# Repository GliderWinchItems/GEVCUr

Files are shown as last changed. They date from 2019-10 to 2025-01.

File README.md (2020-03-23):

# GEVCUr
This goal of this project is to replace the GEVCU unit that control the DMOC (motor inverter) with our unit (hence the 'r') as a step towards developing the master control for the winch. The open source, source code for the GEVCU was used as a guide for dmoc_control.c.

The project is based on the STM32CubeMX, FreeRTOS, and ST DiscoveryF4 board. It uses the control panel developed for the 'mc' (Master Controller) that can be found in GliderWinchCommons (which was based on bare-metal programs).

Electric winch two motor testing 

Two motors are coupled via a Gates belt.  One motor operates in torque mode and the other acts as a regenerative brake in speed mode.  The battery bank supplies power to make up for losses.  Other instrumentation measures drive belt tension, and inverter currents, etc.

WARNING: Use at your own risk. There is a lot of code in this project,and many routines have not been reviewed with others, so bugs, errors, etc., can be expected even though it may appear to "work."

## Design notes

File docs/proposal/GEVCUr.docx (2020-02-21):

SPI and shift-register switches - spiserialparallelSW.[ch]

A. General Strategy

The spi reads from the input shift register while writing to the output shift register. The input shift register loads in parallel from switch inputs, and the output shift register drives FETs that drive LEDs. The switch inputs have pullup resistors and the switch contact closure pulls the input to ground. Therefore, open switches present a one bit. The output shift register drives a FET which pulls a LED via a resistor to gnd, so a one bit in the output turns the LED on.

The spi sends/receives two bytes (currently in the 2/20/2020 repo) then causes an interrupt. The interrupt callback deals with the logic of the switches and restarts another send/receive cycle. With the spi set to the slowest rate the interrupt rate is about 1004 cycles per 100 ms, i.e. approximately 10 cycles per ms. Net, the state of the switches are sampled at about 10K per second.

To deal with this rate, the interrupt callback handling xor’s the input half-word (16b, i.e. two bytes) with the previous half-word, producing a word with bits that are set for switch bits that have changed. If there is no change, no further processing is needed and the next spi cycle is started. If there are changes the switches with changes are updated.

Since a time source is needed for timing the debouncing the spi is used, since the spi interrupt is already present and the rate is relatively constant, the variation only due to the time variations between interrupt and restarting the next cycle. The interrupts are counted down to yield a timing rate of about 100 per sec which is used to time for switch debouncing.

The interrupt handling, therefore, 1) checks for changes in switch bits, handling only those that have changed, and 2) when the countdown counter expires, updates the timing for switches that actively being debounced.

There can be two types of switches. One is the on/off, or pushbutton type, i.e. SPST, and the other is a SPDT which appears to the spi/shift-register as a pair of on/off switches. For the switch pair the combination of the two inputs is used to determine the switch state and debouncing of a single contact is not needed, though at some point timing the indeterminate states as a hardware error check might be added.

B. Switch structs

A switch that is to be used is “instantiated” by a FreeRTOS task by calling an initialization routine. The routine adds a struct to the heap and returns a pointer for that switch to the calling task. The arguments to the initialization routine provides the specifications--

(In the following, the text between “ “ is the element name in the struct.)

(“$” designates arguments in the call to instantiate a switch.)

1. Pointer to next instantiated switch struct, i.e. linked list (“pnext”)

NULL = last on the list of instantiated switches

2. Pointer to next switch that is actively being time for debouncing (“pdbnx”)

NULL = last on the list of active debouncing switches

3. $ Task handle (“tskhandle”)

Null = use the handle of calling task.

4. $ Notification word bit (“notebit”)

This specifies the bit used when the task is notified of a switch status change.

Zero = skip notification

5. $ Switch bit position (“switchbit”)

The bit position in the spi read word for this switch.

6. $ Switch bit position1 (“switchbit1”)

The bit position in the spi read word for this switch for the second in a switch pair, If zero, then the switch is not a pair.

7. $ Type (“type”) (Redundant, unless other possibilities are conjured up.)

0 = SPST, on/off (pushbutton)

1 = SPDT, switch pair

8. Switch status not debounced (“on”)

SPST:

0 = switch closed;

1 = open

SPDT:

0 = 00 both closed *

1 = 01 combination

2 = 10 combination

3 = 11 both open *

* debounced state remains unchanged

9. Switch status debounced (“db_on”)

0 = switch closed;

1 = open

10. $ Mode for debouncing (“mode”)

Here are the current definitions. Only the first three are implemented--

#define SWMODE_NOW 0 // Immediate, w debounce minimum

#define SWMODE_WAIT 1 // Wait until debounce ends

#define SWMODE2_RS 2 // Switch pair R-S flip flop mode

#define SWMODE2_RS_00 3 // Switch pair 00 debounced

#define SWMODE2_RS_11 4 // Switch pair 11 debounced

#define SWMODE2_RS_0011 5 // Switch pair 00 & 11 debounced

11. Debounce working timing counter (“db_ctr”)

This counter counts down the spi time ticks for debouncing.

12.$ Debounce time when closing: (“db_dur_closing”)

This specifies the number of time ticks for a closing event.

13. $ Debounce time when opening: (“db_dur_opening”)

This specifies the number of time ticks for an opening event.

Example of instantiation of a pushbutton switch--

// Control Lever Fullscale Normally open. */

struct SWITCHPTR* psw_cl_fs_no = switch_pb_add(

NULL, /* task handle = this task */

0, /* Task notification bit */

CL_FS_NO, /* 1st sw see shiftregbits.h */

0, /* 2nd sw (0 = not sw pair) */

SWTYPE_PB, /* switch on/off or pair */

SWMODE_WAIT, /* Debounce mode */

SWDBMS(20), /* Debounce ms: closing */

SWDBMS(20)); /* Debounce ms: opening */

Note in the above example “SWDBMS” (SwitchDeBounceMilliseconds) is a macro that converts milliseconds into spi time ticks. The spi time tick is presently 10 ms, so values less than 10 convert to one tick. If no debouncing is to be applied, enter zero instead of the macro. Zero time ticks is handled as a special case and bypasses executing code for the debouncing.

C. Modes

Converting the spi switch bit samples into switch status is different between the the SPST and SPDT switches.

C1. SPST

The switch contacts usually bounce up open and closure, and the duration of bouncing may differ between open and closure so a debounce time is specified for each.

If the switch changes state during active debounce timing, the debounce timer is re-initialized.

There are two modes for debouncing, “SWMODE_NOW”, and “SWMODE_WAIT”. Though not a mode, a third mode is “not debounced” which is executed when the debounce time is zero. A switch bit change is not placed on the list for debounce timing and the output (debounced) state follows the switch open/close. Since debounce times for open and close are specified separately this “zero debounce” can be one or both directions.

The “now” mode the first closure changes the debounced output state and starts the debounce timing. If the switch opens and closes during the debounce timing the output state does not change. Therefore, a very short press of a pushbutton gives one output pulse of duration of the debounce timer. If the press is long the output shows closure immediately and continuously as long as the button remains closed. The logic works the same with the reverse sense of open of close, but the debounce time duration will depend on the duration specified in the instantiation call arguments.

With the “wait” mode output state does not change until the debounce period has expired. A press of a pushbutton, or multiple presses, during the debounce timing do not produce any change in the output state. At the end of the debounce time the output changes to the state of the switch. Since the debounce time is extended each time the switch changes state, rapid pressing of the pushbutton with “wait” mode will indefinitely postpone output as long as the switch transitions take place before the debounce period expires.

C2. SPDT

SWMODE2_RS

The two contacts, i.e. two switches in the spi/shift-register context, determine the change of switch state. In the static state the switch will have one contact closed and the other open. In the transition between states the both may be briefly closed, or both, depending whether the switch is BBM (Break Before Make, Form C), or MBB (Make Before Break, Form D). The BBM case both contacts go open as the switch changes state. In the MBM case both contacts are closed as the switch changes state. Since the contacts might bounce during the transition have the output state only change when there is a open|close or close|open situation and remain the state when there is open|open or close|close, the contact bounce.

If a transition state remains for a long duration that is likely to indicate a hardware failure. For example, both switches open for a long period would indicate that one or both of the switches are not connected. Both closed for a long period would indicate something missing with the pullup resistors.

Adding additional modes to the code to handle these types of situations can be added later.

D. Linked lists & bit mapping

D1. Instantiated switch list--

A “head” pointer points to the first switch struct. (NULL is when the list is empty upon bootup.) The number of switch structs possible can be none (no deboucing, task notification), to as many as there are bit positions, i.e. currently 16 SPST switches possible, or one-half the number of bit positions if all the switches are SPDT.

Individual switch status can be accessed at any time via the pointer (“p→on”) when the switch was instantiated. The word with the spi read word (“spisp_rd[0].u16”) can be read at any time, but it only has the bit status for each shift-register input and SPDT switches will show up as two separate bits, whereas “p->on” will show a number 0-3 for the four possible combinations of the SPDT switch.

D2. Debouncing list--

The “head” to this list (“struct SWITCHPTR* phddb”) is NULL when there are no switches actively debouncing. When a switch bit changes, that switch is added to the the debouncing linked list (provided the specified debouncing time is not zero). Each spi time tick counter, this linked list, if not empty, is traversed, and the debouncing working counters updated. When a counter reaches zero the logic is applied that updates the debounced switch status (“db_on”), and notifies the task, if “notebit” is not zero. A task can access “db_on” at any time via the pointer (“p->db_on”)when the switch was instantiated.

D3. Bit versus struct mapping--

An array of 16 pointers holds pointers to the switch struct so that the position in the array corresponds to the bit position of the switch, as read by the spi.

struct SWITCHPTR* pchange[NUMSWS] = {0};

The spi interrupt xor’s the newly read word with the previous, thus setting bits for switches that have changed. In a single machine cycle the CLZ (count leading zeros) assembly instruction converts the bit position in the xor’d word to the number which is then used an index into the mapping array, thus providing a fast path to the struct for dealing with the change in the switch contact status.

LAST. Items--

Miscellaneous thoughts about the topic.

Array versus heap as needed

Two ways of implementing the structs for each switch is to, 1) define the maximum possible number of structs in common memory, or 2) add structs as needed (via calloc) on the heap. If the structs are placed on the heap, they are not necessarily in consecutive memory locations. To access the structs, given the switch bit position, without a search, an array of pointers that maps bit position to struct location is needed.

However, with all possible structs pre-defined, the mapping array is not needed, saving 4 bytes per switch position, i.e. with 16 switches, 64 bytes. Another 4 bytes are saved in the struct since the list linking the structs is not needed. Net, 128 bytes. Each struct is reduced to 20 bytes. This is weighted against heap method by the number switches actually instantiated, and the number of SPST versus SPDT type switches as the SPDT switch only needs one struct on the heap.

Task versus interrupt handling

The current routine handles the switches during the interrupt. The interrupt priority is set to low priority. The processing is normally very short as most of the time there are no switches changing state and no switches requiring debounce timing. If the application has a large number of switches that change at the same time then some attention to the worst-case interrupt duration and how it might affect RTOS tasks is needed.

If the switch handling is done with a task, then each time the spi has a time tick or switch contact change it has to place the xor’d word on a queue for a task to do the handling. That assures short interrupt handling, but if some of the switches are critical, the switch handling task could be blocked by higher priority tasks. Furthermore, all the spi time ticks and changes result in task context switches.

Extending beyond 16b

Additional shift-registers can be added. This changes the word size in the routines. Beyond 32, the routine has to handle two words when doing xor’s of new versus previous readings since the CLZ instruction works on register, i.e. 32b.

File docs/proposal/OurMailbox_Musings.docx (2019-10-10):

Overview

“Mailbox” thoughts & musings, mainly as an aid to clarifying how to abstract and organize mailboxes in the context of this general project effort.

The notion of adding an ADC based mailbox to the ready-to-debug CAN mailbox code, raised a number of issues. Filtering the raw ADC readings would be expected; and might the logic apply to CAN msgs as well? Calibration is already applied to incoming CAN msgs, but need to be applied to the ADC readings. The parsing of the CAN payload is quite different than for the ADC situation where computations might be required, e.g. conversion of the internal temperature for voltage reference compensation. Filtering is a knotty issue if one considers that more than one type of filtering might be needed for the same readings, i.e. “fast” and “slow” filtering.

Online definitions of mailbox in the context of RTOS says it is a means for passing “messages”, or data exchange. For our purposes, the notion has to do more with making the values of measurements available to one or more tasks than the data where the data may not be some sensor measurement.

A. What the using task might be interested in from a mailboxes--

1. Is this a new reading since the last time I checked?

2. Is this reading “stale” i.e. too old?

3. Is this reading valid, i.e. the status?

4. Being notified when it is updated.

5. The reading filtered either/both--

a. Fast

b. Slow

c. Raw

d. Custom

6. The reading calibrated--

a. Offset

b. Scale

c. For ADC: Temperature compensated

d. For ADC: Sensor voltage compensation

7. Paired readings--

E.g. two different readings in one CAN msg, e.g. shaft speed and shaft encoder counter.

B. Characteristics Our Mailbox (OMBX?) might have--

1. Holds the latest value/reading.

Updates are made without regard to whether the ombx was accessed, i.e. overrun is not an issue.

2. Specific to some reading--

The USPS mailbox receives many different types of messages, that have the common attribute of the same destination address. This concept doesn’t apply the OMBX. E.g. a single OMBX would not combine voltage of 12v supply, drum, #1 tensions, etc. (What about “paired” readings such as shaft speed and encoder count that arrive in one CAN msg? Two maibloxes? One that will handle a float and uint32_t?)

3. Identification

A specific OMBX, or pointer to it, identifies the source of the value/reading. The source could be CAN msgs, or ADC readings, etc.

Implementing this raises the issue of mapping, i.e. a OMBX routing some incoming value/reading, e.g. a CAN msg payload, or element in an array receiving measurements from an ADC scan. These have to be converted from their native form into the common OMBX.

This issue requires some thought. Some typing to develop thinking--

To get a OMBX, e.g., 5v sensor supply voltage, a call to a routine to create an OMBX given the ADC (ADC1, 2, or 3) and ADC array index would be made and a pointer returned that points to the OMBX. The name used for that pointer would be the mnemonic for 5v sensor supply voltage. The call to the routine would include the ADC module handle, and array index. For CAN, a different create routine would be called, but the pointer returned would be the same type. The call would include the CAN control block pointer for the CAN module, CAN ID, and CAN payload type code. Again the naming of the pointer would be the mnemonic for that reading.

If more than one task tried to create the same OMBX the pointer returned would point to the same OMBX, but if notifications were specified in the call, the notification would be added to the list.

The routine creating the OBMX needs to maintain a list of OBMX pointers versus the reading source so that, e.g. a CAN msg after payload conversion can be routed to a mailbox. Similarly, the same for ADC. ADC is easy/fast because the readings are always by position in an array. CAN requires some means of a lookup on CAN module and CAN ID.

Since the number of ADC measurements can not exceed 18 (16 plus internal temp and voltage reference) an array of OMBX for all possible ADC mailboxes could be allocated, i.e. the overhead of a linked list might not be worth the effort. Where the advantage of the array is realized is in the loading of the mailboxes; the index is direct whereas with a linked list the ADC raw array would have to map into the linked list via table of pointers. The linked list would save a little sram, but add flash code.

3. Filtering

At issue is whether to build-in filtering to OMBX, or do it locally in the task. Some tasks might want slow, high filtering, e.g. readings displayed via uart/minicom for human observation, such as load-cell readings. The same readings might also be used where filtering would be fast, e.g. control loop. Should inclusion of filtering in the OMBX include provision for multiple filters.

If filters are included in OMBX, are multiple types needed? A simple one pole IIR filter is simple and easy. One could pass a reading through that filter multiple times for sharper cutoff. There has to be the intermediate storage for each pass ...

The basic OMBX structure could have a pointer to a linked list of these IIR filter structs.

If there is more than one filter, the user would have to make a call to a routine that has the OMBX pointer plus a filter pointer. The filter pointer would have to be included when the OMBX was created, so that would be passed back would be a struct.

Decimation--

If decimation is involved, then most likely notification would associated with it. However, if arrival of a reading is not driving some task, i.e. a notification is give, then task must be polling. If it is polling and checking the filtered reading, then decimation takes place if the reading update is faster than the polling, as well as a resynchronization. Net—including decimation doesn’t make sense at the mailbox level.

4. Calibration

With CAN the approach has been that calibration is done at the sensor node and the CAN msg payload is a calibrated float. With ADC, same approach could be done which requires a routine between the ADC raw readings and the OMBX. The array of ADC readings would be processed to produce an array of calibrated readings before being loaded into a mailbox.

03/07/2019 OurMailbox_Musings.docx Page 3

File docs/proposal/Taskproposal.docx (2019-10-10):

Overview

This presents some ideas on the ‘dynamometer’ project, based on STM32CubeMX, FreeRTOS, and interface & support routines developed in the ‘mxusartusbcan’ project (see ‘Brief.docx’ in ‘msusartusbcan’ directory for more detail). Some of the approaches take into account using the routines beyond the dynamometer project to the winch master controller and other CAN projects. All of this is tentative and details are likely to change as implementation progresses.

A. Infrastructure Tasks

The following outlines how these features developed in the ‘mxusartusbcan’ project are used for the ‘dynamometer’ project.

1. CanTxTask

Passes CAN msgs other tasks want to send to the interface routine (‘can_iface.c’) to the HAL CAN routine (‘stm32F4xx_hal_can’). CAN msgs are sent in CAN priority order.

The CAN msg carries the pointer to the HAL CAN module handle in “our” control block, which sends the CAN msg to the CAN1 or CAN2 modules and hence the CAN bus connected to the module.

2. CanRxTask

In ‘mxusartusbcan’ incoming CAN msgs are placed in a FreeRTOS queue by the functions in the ‘can_iface.c’ routine. For ‘dynamometer’, ‘can_iface.c’ is revised to use a circular buffer and notification to a ‘MailboxTask’ rather than a using a FreeRTOS queue. Besides lower overhead, there can be multiple “take” pointers to the circular buffer, alllowing multiple tasks can access buffered msgs. There is no overwrite protection so the buffer has to be large enough so that the “take” position in the circular buffer for the task with the most delay is not overwritten by “add”. The buffer is set during initialization for ‘can_iface.c’. The ‘take’ pointers are added and initialized by tasks, thereby allowing multiple tasks access to the buffering without the need for a predetermined number to be compiled in to the code.

CAN msgs are “added” to the circular buffer during the callbacks for RX0, RX1, plus the loopback of CAN msgs that were sent if compiled with the option set. The circular buffer is loaded under interrupt, and tasks “take” msgs from the buffer at FreeRTOS task level priority. For this project ‘MailboxTask’, described later, is the main task “taking” msgs from the circular buffer; a gateway-to-PC task would be another common task with a need for dealing with all CAN msgs.

Multiple CAN modules, i.e. CAN1, CAN2, and CAN3 (‘f446 series), is handled by implementing a circular buffer for each CAN module. Partially redundant, the CAN msg struct used in the circular buffer carries the pointer to “our” CAN control block (which includes a pointer to the STM32 CAN control block), and that essentially identifies the CAN module as well.

A time-of-arrival time-stamp in the form of the 32b DTW system counter is included in the CAN msg struct in the circular buffer. Tasks can read this DTW count and check for “stale” readings. This is covered in the description below on ‘MailboxTask’.

B. Project specific tasks

Except for the ‘defaultTask’, these tasks are created “manually”, i.e. not by STM32CubeMX, and reside in the ‘Ourtasks’ directory. STM32CubeMX provides a skeleton task in ‘main’ when the task is specified in the ‘MX setup gui and ‘main’ quickly becomes very large. Most of the code in ‘main’ concerns initialization so having tasks as separate files helps modularize the project.

1. defaultTask

Created: STM32CubeMX. Priority: osPriorityIdle (-3)

The task is always setup by STM32CubeMX when FreeRTOS is selected. It resides in ‘main’. It will be used for the lowest priority computing, such as formatting data for output monitoring on usart6 using ‘yprintf’ (wrapper with semaphores for ‘vsnprintf’), stack high water mark checking, etc.

2. ControlTask

Created: manually Priority: osPriorityNormal (0)

Handles Speed and Torque control using the readings of the two ADC readings. The ADC DMA callback does a 16 reading summation under interrupt followed by a notification. The ControlTask can then do further filtering, calibration, etc., triggered by the notification (see Task02 in ‘mxusartusbcan’).

The ControlTask sends the periodic “keepalive” notifications to the MotorControlTask. The MotorControlTask then shuts down the motors if the notifications are missed. Likewise, the MotorControlTask sending periodic commands to the DMOCs and the DMOCs shutdown if the commands are not received in time.

The ControlTask sends the polling CAN msg; 64/sec. The POD/CAN unit sends back two CAN msgs with the load-cell readings as calibrated floats.

The keepalive notifications could be combined with polling if the DMOC keepalive duration can be set to span the 1/64th sec duration.

For the Master Controller (MC) the routine is interested in readings that might be a combination of the motors, therefore polling of the parameters from the DMOCs by the ‘MotorControlTask’ would be in order.

3. MotorControlTask

Created: manually Priority: osPriorityNormal (0)

This tasks maintains the connection logic for each DMOC state, e.g. “ping” msgs from the DMOCs indicate the DMOC is operational but in a not connected state.

Notification from the ControlTask causes the MotorControlTask to send the speed & torque commands.

4. MailboxTask

Created: manually Priority: osPriorityNormal (3)

The main goal of the Mailbox task is to provide tasks with readings from CAN msgs such that the mailbox has the latest reading, plus a means for detecting if the reading is new, and/or too much time has elapsed since the last update, or a task or tasks, need immediate notification. This would be set to a high FreeRTOS task priority.

Influencing the approach in the following discussion is that it is desirable that ‘MailboxTask’ handle the Master Controller project as well as the ‘dynamometer’ and ‘dynamometer’ serves to refine and prove the approach.

From the ‘ControlTask’ viewpoint, the interest is in “readings,” not CAN msgs. Mailboxes based on readings is a knotty problem for the more general case where CAN msgs might carry more than one reading. E.g. shaft encoding carries a shaft encoder count (signed 32b int) and speed (32b float), combined into one payload since they occur at the same point in time. The CAN msg would need to update two mailboxes.

Rather than deal with the multiple readings per CAN msg issue, the CAN msgs could be limited to just one reading per CAN msg. This increases the CAN bus load a bit. In the case of battery cell voltages the inefficiency makes it a dubious tradeoff. A compromise is for the mailbox to allow for two readings.

Another complicating issue is if the control program is using a a mailbox, e.g., cable speed, it the source of the reading changes when the drum changes, i.e. the ‘MailboxTask’ would be updating the cable speed mailbox from different CAN msg IDs, conditional upon the active drum. However for the retrieve, where all drums might be active, (but in low tension, low speed), the control program would be interested in all mailboxes. This latter situation opts for multiple mailbox for the same class of reading, and the control program selects the mailbox based on active drum. (The same issue applies to multiple motors and battery banks.)

At this point, the approach to be taken is to take incoming CAN msgs; look them in a table which identifies them as associate with a mailbox. Those not found in the table are discarded. Tasks have a pointer to mailboxes and a mailbox can be used by multiple tasks, so it provides a means for distributing CAN msgs to unrelated tasks. (A separate task would be sending all CAN msgs to the PC for the gateway function, if the PC gateway is included. When all CAN msgs are to be used the ‘MailboxTask’ isn’t needed and the CAN msgs can be taken directly from the circular buffer receiving the incoming CAN msgs.) (Another consideration is the CAN bus gateway, where incoming CAN msgs on one bus are selectively sent to the other bus or buses if there are three CAN modules. This is a mailbox type of process where the CAN id has to be identified and either discarded or directed to another CAN bus.)

A CAN msg found in the table has its payload parsed, according to the code in the table. PAYLOAD_TYPE_INSERT.sql already exists and carries the name v code for the payload types (26) encountered so far. This table also has to associate the CAN msg with a mailbox. A list of mailboxes could be maintained by adding a .sql file to the database that associates a mailbox name with CANID, and payload reading. Multiple readings in a CAN msg would have multiple entries in this table. The project would have a table using the #defines generated from the database tables that specifies the mailbox name. In the case of multiple drums, there would be multiple tables of identical layout (i.e. the same struct) that can be selected by drum number.

Moving to some details about some in progress work on implementation--

Work on ‘MailboxTask’ implementation began with the a CAN msg with limited payload decoding mailbox rather than “readings” mailbox. As described above in A.2., CanRxTask, the Mailbox task gets pointer to CAN msgs on the circular buffer of incoming CAN msgs. This CAN msg has the CAN id, dlc, payload, “our” control block pointer which identifies the CAN module, hence bus, plus the 32b DTW time-of-arrival timestamp. The mailbox struct includes an msg update counter, and pointer to a linked list of notification blocks; if more than one task needs to updated when the CAN msg arrives the linked list provides the task-handle and notification bit for the each of the task notifications.

When a CAN msg is added to the circular buffer in ‘can_iface.c’, a notification to ‘MailboxTask’ is made. ‘MailboxTask’ takes a CAN msgs from the circular buffer and does a lookup in the list of CAN bus, and CAN ids. If it appears in the list, it converts the payload and loads the mailbox with the payload converted to readings, plus the time-of-arrival DTW and increments an update counter in the mailbox. If the mailbox has the task handle and notification bit setup, a notification is made.

Since there can be multiple tasks that need notification when a mailbox is updated, a linked list for each mailbox provides a means of stepping down the list making notifications for each task. For tasks that do not need a notification access can be made at any time and the time-of-arrival or update counter used to determine if the reading is stale or now. To do this each tasks needs to have the pointer to the mailbox. That pointer can be retrieved by a call to “add a mailbox”. The call to “add a mailbox” includes the CAN ID, so the initialization can check for duplicates, the existing pointer is returned and a new mailbox not created, however if a notification is desired, the call to “add a mailbox” includes the notification bit to be used it is added to the linked list.

There are several levels of initialization involved. The first is the creation of ‘MailboxTask’ which is performed in ‘main’ before the task scheduler is started. The initialization would include a call to ‘can_iface.c’ to add a “take” pointer for the circular buffer of CAN msgs. When ‘MailboxTask’ has started and is in the endless loop it receives a notification and does a ‘while’ to remove CAN msgs until it is caught up.

The list of CAN bus and CAN ids to be selected is generated by the tasks during initialization, after the task starts and before the endless loop, or after the task was created but before the scheduler started. The list is sorted so that the binary lookup can executed rapidly. For eight drums the list could in the 30-40 range. For a single drum the binary lookup wouldn’t pay. For the dynamometer, the list is probably about 6 per CAN bus and a binary search isn’t warranted. The task level initialization includes the notification bit to be used by the task if notifications are used, and as such requires that the task handle has been created, hence this is most conveniently done after the task has just started.

When a task polls, it may want to know if the mailbox reading is too old, in which case it can check the current DTW time count versus the one stored in the mailbox. Or, it may need to know if there is a new reading, in which case the task compares the mailbox update count with the previous count which was saved locally. Any number of tasks can be using the CAN mailbox in these two modes.

If the notification handle is NULL or the notification bit word zero, ‘MailboxTask’ would not execute a notification. However, if given the task and notification bit was set, the task would be notified. This would unblock the task waiting with on ‘NotifyWait’ and the mailbox would be dealt without further delay. The notification bit(s) that are found to be set when the task unblocks identify the mailbox(es) that were in the notifications.

A further detail in the implementation is to have an array of pointers to the mailbox structs (which were calloc’d). When the mailboxes are created by calls at the task level initialization, the mailbox is loaded with the CAN id and CAN control block pointer (CAN module identification), and the pointer added to the array. The array of pointers is sorted on CAN id. The array of pointers is then used for the lookup with CAN that was taken off the circular buffer. CAN msgs not in the list are simply ignored for mailbox updating.

Another possibility: Do this as two steps. The first step is to select CAN msgs for a task or set of related tasks, and have a second level deal with conversion to mailboxes, or something else. If the processor/board is handling more than one winch function then some of the tasks are not interested in some of the CAN msgs. Rather than having each function go through their list of CAN msgs for each arriving CAN msg, this approach would supply each task with only the CAN msgs of interest to the task.

Simplifications from compromises--

The pure form is to have a mailbox only contain a single reading, and be agnostic entirely to CAN msgs. With this a lot of details get push out of the “user” task and in to the infrastructure tasks. If instead of a mailbox holding just one reading, the mailbox holds the readings for a CAN msg, the naming and association of mailbox readings with CAN ids can be eliminated. That still leaves the problem of various payload formats, e.g. the reading is a float, but the four bytes for the float might start at payload[0], [1], or [2]. If the bytes preceding the float were jettisoned then a single four byte element in the mailbox would suffice. If a second four byte element is added, two readings could be accommodated and this would cover most cases. Furthermore, if the readings are all converted to ints/uints and floats and presented in a union the “user” task can access them, but needs to know which type to use. E.g. suppose during the task initialization it “adds” a mailbox, which returns a pointer to the mailbox, e.g. p_tension. The mailbox might ad accessed like this --

ften_belt = p_tension->u.f1; // Get first float

ften_mtr = p_tension->u.f2; // Get second float

This requires the using program to know more about the payload than if the mailbox was simply a single reading of ‘tension_belt’.

5. GatewayTask

Created: manually Priority: osPriorityNormal (0)

This task takes incoming CAN msgs from the circular buffer with CAN msgs; converts them to the ascii/hex format and sends them out on the high speed usart (usart2 @ 2E6 baud) to the PC . (‘gateway_CANtoPC’, used in Task03, in ‘mxusartusbcan’.)

Ascii/hex CAN msgs coming in from the PC are converted to the binary CAN format and passed on to CanTxTask for sending.

To deal with the CAN1/CAN2 issue ascii/hex format robs the low two bits from the sequence number of the CAN msg and uses that for a CAN1/2/3 identifcation (STM32F4 series has two CAN modules, and the STM32F7 has three) . NOTE: this requires some modification of ‘cangate’ to either have a CAN1/2/3 version, or way to avoid the original ‘cangate’ from flagging a sequence number error.

An alternative is to use the gateway to the PC in a one CAN bus mode and avoid the CAN1/2 issue, but requires two gateways or gatewayfunctions (i.e. one could run two usarts to the PC, each carrying traffic for one CAN bus).

Use of the usb CDC (virtual com port) for gateway purposes requires some additional work, as the buffering/interrupt/polling is somewhat different with the STM HAL routine for usb-cdc and the usart routines.

‘dynamometer’ STM32CubeMX project Page 6

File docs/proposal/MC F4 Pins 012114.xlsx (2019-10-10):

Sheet: Sheet1
Use | Ports | Our Use Function | Board Function 1 | P1 | P2 | Other Functions - Comments
Input Switches and Output LEDs (GP and SPI) | PB12 | SPI2_NSS | Free I/O | 36 |  | JTDI/, SPI3_NSS/, I2S3_WS/, TIM2_CH1_ETR/, SPI1_NSS
 | PB13 | SPI2_SCK/ | Free I/O | 37
 | Other functions of PB3: JTDO/, TRACESWO/, SPI3_SCK/, I2S3_CK/, TIM2_CH2/, SPI1_SCK
 | PB14 | SPI2_MISO/ | Free I/O | 38
 | PB15 | SPI2_MOSI | Free I/O | 39
ADCs (3 allocated) | PC1 | ADC123_IN11 | Free I/O | 7
 | PC2 | ADC123_IN12 | Free I/O | 10
 | PC4 | ADC123_IN14 | Free I/O | 20
CANbus | PD0 | CAN1_RX | Free I/O |  | 36
 | PD1 | CAN1_TX | Free I/O |  | 33
UART (Bootloader) | PA9 | USART1_TX | VBUS_FS |  | 44 | Bootloader assumes serial loader is on PA9 & PA10 - conflicts with USB
 | PA10 | USART1_RX | OTG_FS_ID |  | 41
UART (GPS) | PA2 | USART2_TX | Free I/O | 14
 | PA3 | USART2_RX | Free I/O | 13
UART (LCD) | PD8 | USART3_TX | Free I/O | 40
 | PD9 | USART3_RX | Free I/O | 41
GPS 1PPS | PA1 | TIM5_CH2 | Free I/O | 35
Beeper | PB8 | TIM10_CH1 | Free I/O |  | 43
PWM (Contactor) | PE5 | TIM9_CH1 | Free I/O |  | 14
PWM (Panel Dim) | PE6 | TIM9_CH2 | Free I/O |  | 11
Audio (ISI and SPI) | PB6 |  | Audio_SCL
 | PB9 |  | Audio_DSA
 | PC7 |  | I2S3_SCK
 | PC10 |  | IS23_SCK
 | PC12 |  | IS23_SD
 | PA4 |  | I2S3_WA
 | PD4 |  | Audio_RST
 | PC3 |  | PDM_OUT
 | PB10 |  | CLK_IN
Accelerometers | PA7 |  | SPI1_MOSI
 | PA5 |  | SPI1_SCK
 | PE0 |  | MEMS_INT1
 | PE1 |  | MEMS_INT2
 | PE3 |  | CS_I2C/SPI
 | PA6 |  | SPI1_MOSI
USB_OTG | PC0 |  | OTG_FS_PowerSwitchOn
 | PA9 |  | VBUS_FS
 | PA10 |  | OTG_FS_ID
 | PA11 |  | OTG_FS_DM
 | PA12 |  | OTG_FS_DP
 | PD5 |  | OTG_FS_PverCurrent
LED (Green) | PD12 |  | GPIO
LED (Orange) | PD13 |  | GPIO
LED(Red) | PD14 |  | GPIO
LED(Blue) | PD15 |  | GPIO
Reset PB | NRST |  | NRST
User PB | PA0 |  | GPIO
Denotes a possible conflict
Check appropriate timers and channels have been used
Last Update: 1/21/2014

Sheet: Sheet2
PA1
PA10
PA10
PA11
PA12
PA15
PA2
PA2
PA3
PA3
PA4
PA5
PA6
PA7
PA8
PA9
PA9
PB10
PB11
PB3
PB4
PB5
PB6
PB9
PC0
PC10
PC12
PC3
PC3
PC4
PC7
PD0
PD1
PD10
PD4
PD5
PD8
PD9
PE0
PE1
PE10
PE11
PE12
PE13
PE14
PE3
PE7
PE8
PE9

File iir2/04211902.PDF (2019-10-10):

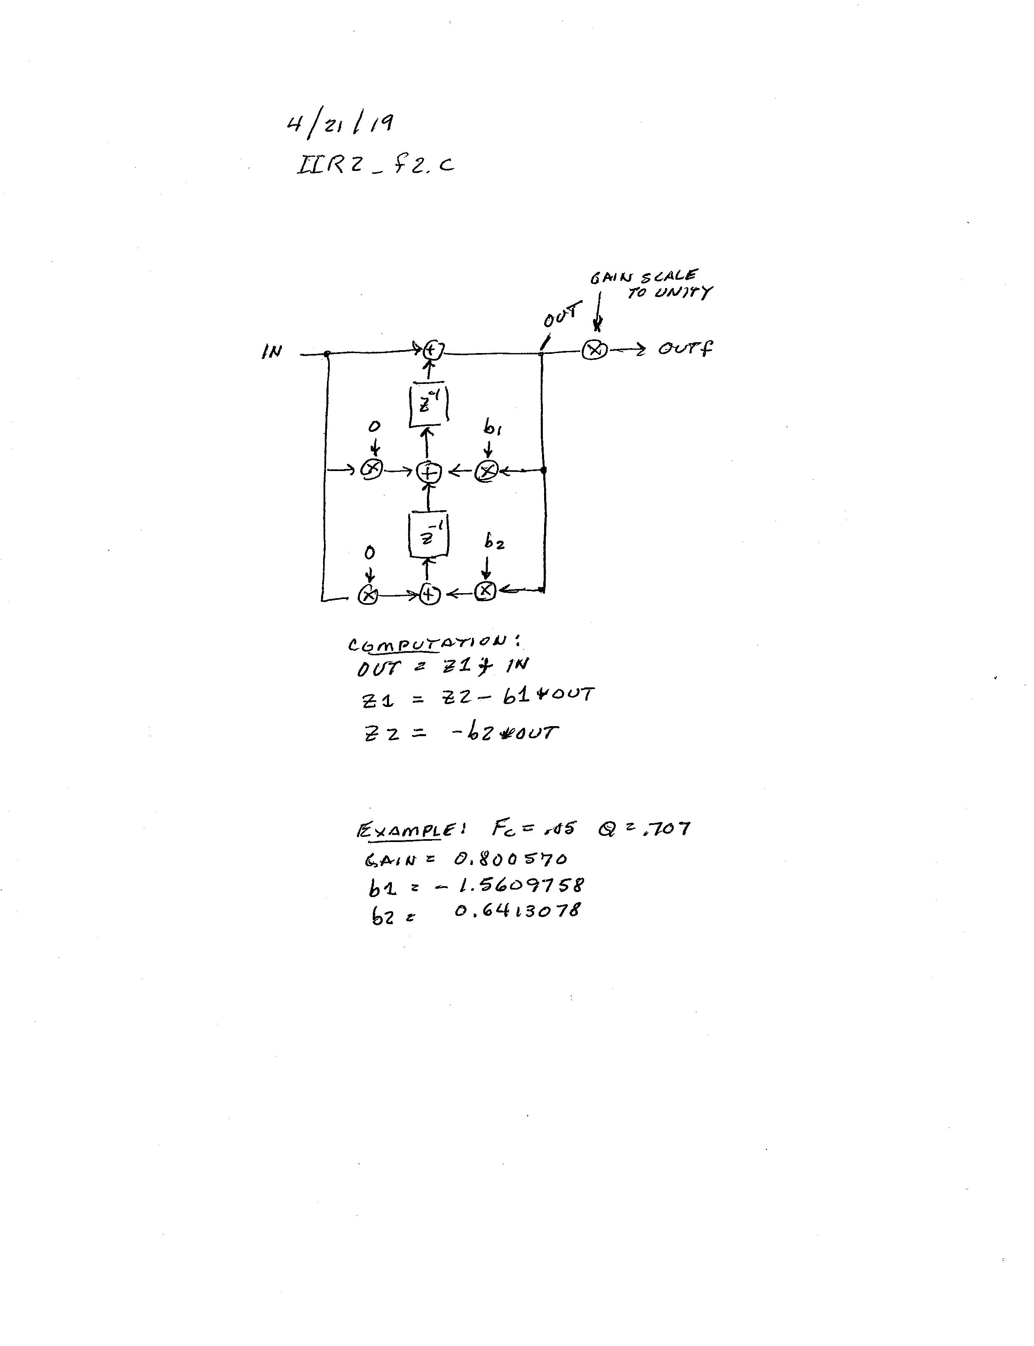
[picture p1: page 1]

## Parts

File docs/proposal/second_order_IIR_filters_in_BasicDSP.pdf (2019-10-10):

## Second-order IIR filters in BasicDSP (http://www.google.com/search?q=basicDSP)

by Niels A. Moseley PE1OIT

Second-order filters offer a sharper frequency response compared to the first-order filter. First order filters, which have a 6 dB per octave slope, are often used for quick-and-dirty smoothing. If you want a steeper slope, such as 12 dB per octave or higher, you need a higher order filter.

A simple way to achieve a higher order is to put two first-order filters in series. This is similar to putting two analog RC filters in series. Unfortunately, this isn't the best filter you can make, given the number of components. Better filters (fewer components) can be made by including an inductor L, which leads to an RLC filter.

The digital equivalent of an RLC filter is the second-order IIR filter:

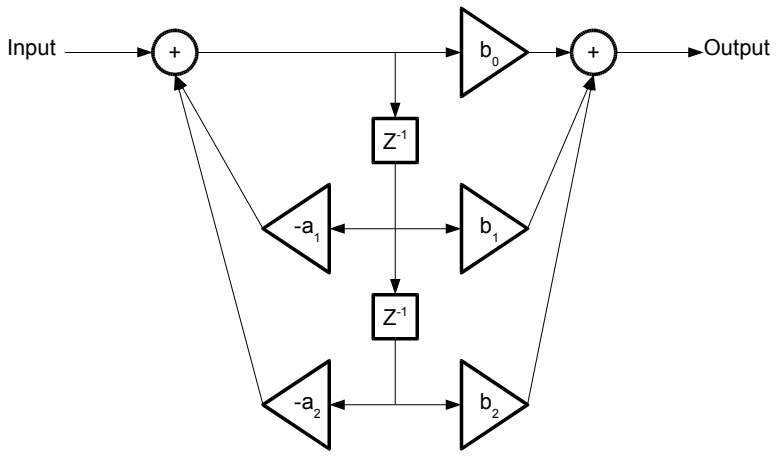
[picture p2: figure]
Input; Output

The 'Z⁻¹' blocks are a 1-sample delay. The following BasicDSP script implements this filter:

temp = f_in - a1*state1 - a2*state2
f_out = b0*temp + b1*state1 + b2*state2
state2 = state1
state1 = temp
,where 'state1' and 'state2' are the values stored in the 1-sample delay blocks. The input and output of the filter are 'f_in' and 'f_out', respectively.

For lowpass filters, the filter coefficients (a1, a2, b0, b1 and b2) can be calculated using the following formulas [1]:

pi = 3.1415927
w0 = 2*pi*f0/FS; (where f0 is the desired cutoff frequency, and FS is the sample rate)
alpha = sin(w0)/(2*Q); (where Q is typically 0.5*sqrt(2)=0.707)
b0 = (1–cos(w0))/(1+alpha)
b1 = 2*b0
b2 = b0
a1 = -2*cos(w0)/(1+alpha)
a2 = (1-alpha)/(1+alpha)

Combining the filter and the calculating of the filter coefficients, we can make a second order filter where the cutoff frequency f0 is settable through slider1:

samplerate = 44100;
f_in = in;

; calculate filter coefficients w0 = 3.1415927*slider1
alpha = sin(w0)/(2.0*0.707) b0 = (1-cos(w0))/(1+alpha)
b1 = 2*b0
b2 = b0
a1 = -2*cos(w0)/(1+alpha)
a2 = (1-alpha)/(1+alpha)

; calculate filter
temp = f_in - a1*state1 - a2*state2 f_out = b0*temp + b1*state1 + b2*state2 state2 = state1
state1 = temp

out = f_out * 0.1
Here's a screenshot of the filter spectrum (input = impulse & slider1 = 0.2476):

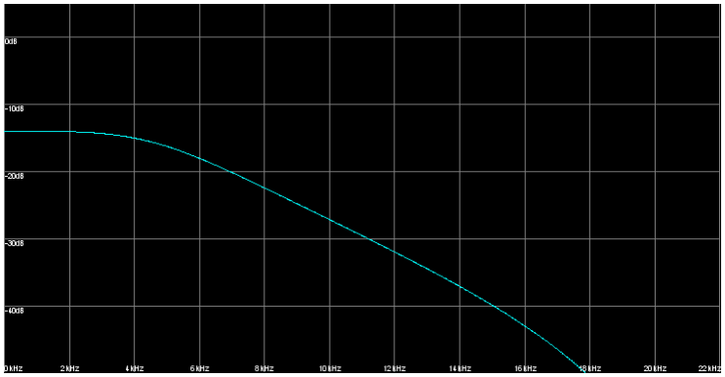
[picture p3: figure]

References:

[1] Filter design equations http://www.musicdsp.org/files/Audio-EQ-Cookbook.txt

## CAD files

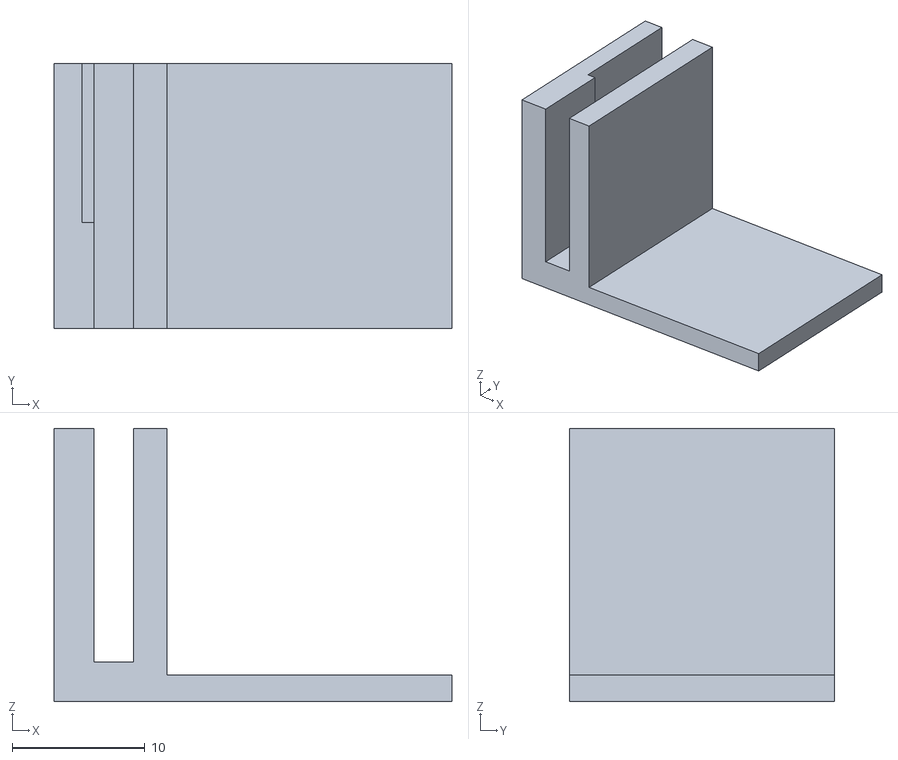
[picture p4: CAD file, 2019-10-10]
hw/openscad/ftdi_clip.stl
30.0 x 20.0 x 20.6

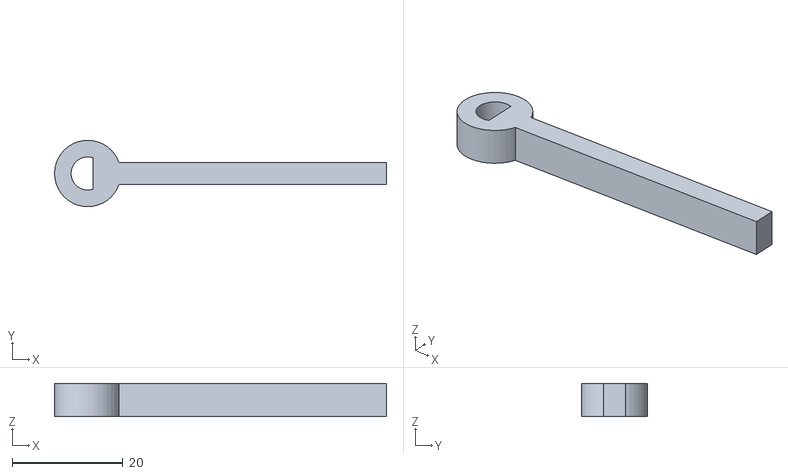
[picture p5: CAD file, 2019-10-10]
hw/openscad/pot_mnt2lvr.stl
60.0 x 12.0 x 6.00

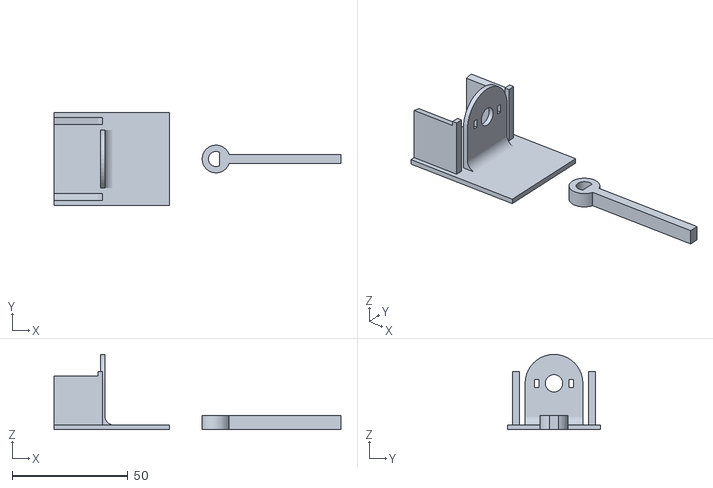
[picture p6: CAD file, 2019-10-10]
hw/openscad/pot_mnt2.stl
124.0 x 40.0 x 32.5

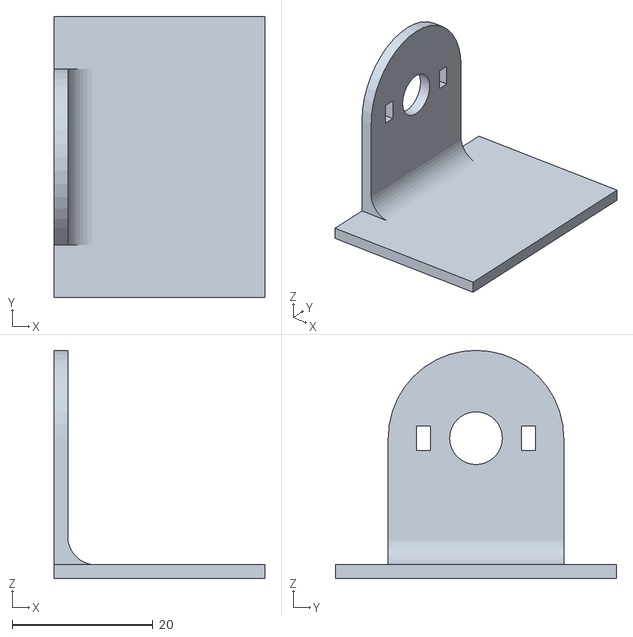
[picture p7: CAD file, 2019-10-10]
hw/openscad/pot_mnt.stl
30.0 x 40.0 x 32.5

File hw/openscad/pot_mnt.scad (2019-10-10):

/* File: pot_mnt.scad -- Stacked
 * Clip for pot mount for Control Panel simulator
 * Author: deh
 * Latest edit: 20191002
 */

include <../../../../git_3D/scad/library_deh/deh_shapes.scad>

 $fn = 40;
 
 thick = 2.0;
 
 /* ***** fillet *****
 * r = radius of fillet
 * l = length of fillet
 fillet (r,l);
*/
module fillet(r,l)
{
   difference()
   {
     union()
     {
       cube([2*r,2*r,l]);
     }
     union()
     {
       translate ([r,r,0])
           cylinder(d = 2*r + 0.1, h = l, center = false);
       translate([r,0,0])
           cube([r,2*r,l],center = false);
       translate([0,r,0])
           cube([2*r,r,l],center = false);
     }
   }
}

module pot_mnt (a)
{
    offset = 9-1.5;    

	translate(a)
		/* ***** eyebar *****
 * rounded bar with hole in rounded end
 * module eye_bar(d1, d2, len, ht)
d1 = outside diameter of rounded end, and width of bar
d2 = diameter of hole in end of bar
*/  
    difference()
    {
        union()
        {
            eye_bar(25, 7.5, 20, 2);
            
            translate([18,12.5,2])
            rotate([90,-90,0])
            fillet(4,25);
        }
        union()
        {
            translate([0,offset,0])
                cube([3.5,2.0,20],center=true);
            translate([0,-offset,0])
                cube([3.5,2.0,20],center=true);

        }
    }
}

module plat(a)
{
    translate(a)
        cube([30,40,2],center=false);
}

rotate([0,90,0])
    pot_mnt([-20,0,0]);

plat([0,-20,0]);

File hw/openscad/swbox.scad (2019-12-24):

/* File: swbox.scad
 * Box to hold perfboard with shift register w leds and switch header
 * Author: deh
 * Latest edit: 20191214
 */
 
 $fn = 40;
 
 // Perfboard dimensions
 pbdel = 0.5;  // A little extra
 pbx  = 80 + pbdel; 
 pby  = 40 + pbdel;
 pbz  = 1.5;  // board thickness
 pbz1 = 4.2;  // bottom to top of wiring
 
// Box 
 boxwall = 6;
 boxfloor = 4;
 boxx = pbx + boxwall*0.5;
 boxy = pby + boxwall*0.5;
 boxz = 24;
 
 // Main box cutout
 boxqx = pbx - boxwall*0.5;
 boxqy = pby - boxwall*0.5;
 
 // Switch cable cutout
 swcofx = 37;
 swcofz =  2;
 swcx = 6;
 swcz = 20;
 
 // spi cable cutout
 spiofx = 42;
 spiofz =  2;
 spix = 20;
 spiz = 10;
 
 // Post height
 pstz = boxz; // Height
 pstd = 6;  // Diameter
 paa = 1.1; // Post center offset
 
 
 module post(a)
 {
     translate (a)
     {
        translate([0,0,boxz-pstz])
        difference()
        {
            union()
            {   
                cylinder(d=pstd,h = pstz,center=false);
            }
            union()
            {
                translate([0,0,pstz-30])
                cylinder(d=2.9,h=60,center=false);
            }
        }
    }
 }
 
 module mainbox()
 {
     difference()
     {
         union()
         {
             cube ([boxx,boxy,boxz],center=false);
             post([    -paa,    -paa,0]);
             post([boxx+paa,    -paa,0]);
             post([boxx+paa,boxy+paa,0]);
             post([    -paa,boxy+paa,0]);
         }
         union()
         {
             // Main cutout
             translate([boxwall*0.5,boxwall*0.5,boxwall*0.5])
                cube([boxqx,boxqy,50],center=false);
             
             // Recess for perf board
             translate([boxwall*.25,boxwall*.25,boxz-pbz])
                cube([pbx,pby,50],center=false);
             
             // Switch cable
             swcq = boxfloor + swcofz;
             translate([boxwall*.25+swcofx,-4,swcq])
                cube([swcx,20,swcz],center=false);
             
             // spi cable
//             spiq = boxfloor + spiofz;
//             translate([boxwall*.25+spiofx,boxy-8,spiq])
//                cube([spix,30,spiz],center=false);
             
         }
     }
 }
 cvrz   = 4;      // Cover thickness
 cvrofx = 10 + boxwall*.25; // pushbutton window offset
 cvrofy = 25 + boxwall*.25; // pushbutton window offset
 cvrx   = 60;    // Length of pushbutton window
 cvry   = 10;    // Width of pushbutton window
 cvrdel = 2.5;   // Overlap a edge
 
 module cvrpost(a)
 {
     translate (a)
     {
        translate([0,0,0])
        difference()
        {
            union()
            {   
                cylinder(d=pstd,h = cvrz,center=false);
            }
            union()
            {
                translate([0,0,-.5])
                cylinder(d=3.2,h=8,center=false);
            }
        }
    }
 }
 cvrw = 1.5;
 cvrlj = 2.0;
 cvrlh = cvrz + cvrlj;
 
 module cvrlip(a,r,l)
 {
      translate (a)
     {
        translate([0,0,cvrlj])
        difference()
        {
            union()
            {   
                translate([0,0,0])
                cube([l,cvrw,cvrlh],center=true);
            }
            union()
            {
            }
        }    
    }
 }
 
 // Toggle switch hole in cover
module togglehole(a)
{
   translate(a)
    cylinder(d = 6.4, h = 20, center=true);
} 
 
 module cover(a)
 {
     translate(a)
     {
         difference()
         {
             union()
             {
                cube ([boxx,boxy,cvrz],center=false);
                cvrpost([    -paa,    -paa,0]);
                cvrpost([boxx+paa,    -paa,0]);
                cvrpost([boxx+paa,boxy+paa,0]);
                cvrpost([    -paa,boxy+paa,0]);
                 
//cvrlip([boxx/2,-cvrw,0],[0,0,0],boxx-2*boxwall-8);                 
             }
             union()
             {
                // Recess in cover
//                translate([boxwall*.25+cvrdel*.5,boxwall*.25+cvrdel*.5,0])
//                    cube([pbx-cvrdel,pby-cvrdel,cvrz-1.5],center=false);
                 
                // pushbutton plate window
                 translate([cvrofx,cvrofy,-1])
                    cube([cvrx,cvry, 30],center=false);
                
                // Holes for toggle switches
                 inc = 18; qx = (pbx - 3*inc)/2; qy = 13; 
                 togglehole([qx+(0*inc),qy,0]);
                 togglehole([qx+(1*inc),qy,0]);
                 togglehole([qx+(2*inc),qy,0]);                 
                 togglehole([qx+(3*inc),qy,0]);
             }
         }
     }
 }

 
 pinx = 7.0;    // sw pin spacing x direction
 piny = 4.4;    // sw pin spacing y direction
 
 swplatex = 10.0 ;  // width
 swplatey = 8.0;
 sidey = 15.0;
 
 pwinx = 1.8;
 pwiny = 1.5;
 
 module pbhole(a)
 {
     translate(a)
     {
        cube([pwinx,pwiny,20],center=true);
     }
 }
 module pbholes(a)
 {
     translate(a)
     {
        pbhole([   0,   0, 0]);
        pbhole([pinx,piny, 0]);
        pbhole([pinx,   0, 0]);
        pbhole([   0,piny, 0]);
     }
 }
 
pbhx = 70;
pbhy = 20;
pbhz = 1.4;
 module pbplate(a)
 {
hofx = 6;
hofy = 8;     
incx = 16;
     
     translate(a)
     {
         difference()
         {
            cube([pbhx,pbhy,pbhz],center=false);
             
            union()
            {
             pbholes([hofx+0*incx,hofy,0]);
             pbholes([hofx+1*incx,hofy,0]);
             pbholes([hofx+2*incx,hofy,0]);
             pbholes([hofx+3*incx,hofy,0]);             
            }
        }
     }
 }
 
// mainbox();
 
// rotate([180,0,0])
//   cover([0,0,35]);
 
 pbplate([10,20,45]);

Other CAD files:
hw/openscad/ftdi_clip2.stl
hw/openscad/pot_mnt2.scad
hw/openscad/ftdi_clip.scad
hw/openscad/ftdi_clip2.scad

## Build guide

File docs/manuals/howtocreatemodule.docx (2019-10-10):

# GEVCU

Generalized Electric Vehicle Control Unit

# Programmer Checklist

# For Adding Object Modules to the

# GEVCU Software

The Generalized Electric Vehicle Control Unit software is open source and object oriented. It was originally developed to control the Azure Dynamics model 645 Digital Motor Controller (DMOC) – a 3-phase inverter/controller used with the Siemens 1PV5134 motor on the Azure Dynamics eTransit Connect.

The DMOC645 was CAN controlled and did not feature any inputs for throttle, brake or other inputs and outputs. The eTransit Connect Vehicle Control Unit (VCU) performed that duty. Lacking the VCU, we had to develop a VCU from scratch capable of providing the necessary CAN messages to the DMOC645 to in turn control the motor.

The concept of a GENERALIZED VCU specifically for electric vehicles derived from the many different types of cars that would be converted to electric drive using this drive system. But from the beginning we saw the need to drive other types of controller/inverters and indeed interact with other devices such as chargers, DC-DC converters, and battery management systems.

So a central tenet of the GEVCU was a very object oriented approach that would easily allow the addition of new classes and new objects to accommodate different equipment. The goal of course to limit software changes to just the additional object added to accommodate the new equipment.

Some wins and some losses. Indeed GEVCU now supports the BRUSA drive train, the CODA/UQM drive train, and more are envisioned and already a series of chargers, BMS, and other devices have been added.

But along the way, we encountered several targets of opportunity that were just two good to pass on, that tend to complicate the easy addition of object modules.

CREATE OBJECT MODULE

TASKING AND PRIORITIES.

PERSISTENT CONFIGURATION STORAGE

MULTIPLE DEVICES ON CAN

# CREATING AN OBJECT MODULE

You create an object module basically by adding a .cpp and .h file to the program set defining your object module. The best way is to copy one from a similar device. If you are doing an object module for a motor controller, a good start would be to copy and rename the DMOC645 motor controller object module held in DmocMotorController.cpp and DmocMotorController.h

Let’s call the new module EVIC and we’ll rename the copied files EVIC.cpp and EVIC.h.

To add these to the program, you basically do two things.

1. Add an include for EVIC.h in the GEVCU.h header file.

#include "EVIC.h"

2. Add a createObjects entry in the main program file GEVCU.ino

void createObjects() {

PotThrottle *paccelerator = new PotThrottle();

CanThrottle *caccelerator = new CanThrottle();

PotBrake *pbrake = new PotBrake();

CanBrake *cbrake = new CanBrake();

DmocMotorController *dmotorController = new DmocMotorController();

CodaMotorController *cmotorController = new CodaMotorController();

DCDCController *dcdcController = new DCDCController();

BrusaMotorController *bmotorController = new BrusaMotorController();

ThinkBatteryManager *BMS = new ThinkBatteryManager();

ELM327Emu *emu = new ELM327Emu();

ICHIPWIFI *iChip = new ICHIPWIFI();

EVIC *eVIC = new EVIC();}

Here, we instantiated the object eVIC of type EVIC as a new instance of EVIC().

Our eVIC object is now part of the program and enjoys all the rights and privileges of other objects of the program.

Note that most objects you will create will actually be child objects of more generalized parent objects. A motor controller object, for example, usually inherits from MotorController and from CanHandler. Much of the basic work common to all motor controllers is already done for you in the parent and standard variables are already there for you to update from your own specific code. You also generally must inherit from CanHandler to be able to catch and send CAN messages in your object.

So you will find something like this in your .h file.

class EVIC: public Device, CanObserver {

public:

Here, in EVIC.h, we are defining a new class EVIC which inherits from the generic Device class but also from CanObserver. A motor controller might be better to inherit from MotorController and CanObserver.

Obviously, you will likely have to rename almost all the class references in your .cpp and .h files.

# TASKING AND PRIORITIES

We hesitate to claim we have duplicated Linux and a real time operating system here. But the Arduino Due does sport an interesting set of clocks – 3 of them actually – each with 3 configurable interrupt timers for a total of 9 timer interrupts.

Inverter/controllers are operating powerful motors in real time and can be a bit demanding in that they want constant attention – regularly updated CAN control messages or they tend to shut down as a safety consideration. So inverters need the highest priority.

GEVCU does provide information to the user and allows configuration either by USB serial port or via a wireless web site. But while driving down the road, it would be quite normal for NO ONE to be using this at all to configure the system. So this is an example of a very low priority. Chargers and Battery Monitors and so forth would fall somewhere in between.

So we have developed a module called a TICK HANDLER. Your object module must register with this TICK HANDLER and then provide a public method, also termed TICKHANDLER to perform its duties as it can when the TICKHANDLER passes it a tick (timeslice).

You can think of your tickhandler as the LOOP routine in the Arduino Sketch/Processing environment or more traditionally MAIN.

To register your object with the tickhandler, the following general steps are in order.

1. Add a tickhandler DEFINE for your object to config.h file to set your tick interval in microseconds.

#define CFG_TICK_INTERVAL_EVIC 100000

Here, we define a tick interval for EVIC to call it every 100,000 microseconds (100 milliseconds)

2. Add a setup function to your object module establishing tickhandler

void EVIC::setup()

{

TickHandler::getInstance()->detach(this);//Turn off tickhandler

(Any number of other setup statements)

TickHandler::getInstance()->attach(this, , CFG_TICK_INTERVAL_EVIC);

}

In case our tickhandler is on, we turn it off. Perform any other setup functions desired. And then attach the tickhandler using the DEFINE from config.h.

3. Add a tickhandler function to your object module

void EVIC::handleTick()

{

sendCmdCurtis();

sendCmdOrion();

}

Here, we have a short function that calls two other functions. Each of those create and send a CAN command. So each 100 ms, the tickhandler will call the object function handleTick, which will send two CAN messages and return.

4. In your object module .h file, add the following includes:

#include "config.h"

#include "TickHandler.h"

# PERSISTENT CONFIGURATION STORAGE

Almost all modules in the GEVCU have some level of need to store information between operating sessions. This may be system data that you want to maintain from startup to startup such as accumulated Ampere-Hours or peak temperatures.

But almost all devices have some configuration options that end users can adjust to modify the operation of the software.

The Arduino Due ARM3 processor gives us very good power and speed for the VCU function, but it does not provide an EEPROM and the use of flash memory for persistent data has a problem in that it is totally erased if the software is updated.

So GEVCU has a 2Megabit (256kbytes) EEPROM provided just for such persistent data.

In coding independent objects that could be enabled in a variety of combinations, we have to have some means of rationalizing who stores what at what address and when. Otherwise, objects would be overwriting each other’s data.

Further, EEPROM’s have a defined write life. Not quite the issue it was originally, it is still nice to limit the number of writes so that the same data is not rewritten every 30 msec.

We do this with a device termed a MEMCACHE. An object has to register with DEVICES and is allocated a block of memory in MEMCACHE. The data in MEMCACHE is then recorded to EEPROM periodically. And it is loaded into MEMCACHE on startup. In this way, you can save your configuration data and load it again on the next startup.

1. Each device should create a configuration class that inherits from DeviceConfiguration. This will be in your .h file.

class EVICConfiguration: public DeviceConfiguration {

public:

};

2. The loadConfiguration() and saveConfiguration() methods of DmocMotorController and MotorController can be used as a reference for how to load and save configurations.
3. PrefHandler handles the memcache for various devices. Each device needs its own unique name and id number. These are held in the file DeviceTypes.h

enum DeviceId { //unique device ID for every piece of hardware possible

DMOC645 = 0x1000,

BRUSA_DMC5 = 0x1001,

CODAUQM = 0x1002,

BRUSACHARGE = 0x1010,

TCCHCHARGE = 0x1011,

LEAR=0x1012,

THROTTLE = 0x1030,

POTACCELPEDAL = 0x1031,

POTBRAKEPEDAL = 0x1032,

CANACCELPEDAL = 0x1033,

CANBRAKEPEDAL = 0x1034,

EVICTUS = 0x4400,

ICHIP2128 = 0x1040,

DCDC = 0x1050,

THINKBMS = 0x2000,

SYSTEM = 0x5000,

HEARTBEAT = 0x5001,

MEMCACHE = 0x5002,

PIDLISTENER = 0x6000,

ELM327EMU = 0x650,

INVALID = 0xFFFF

};

Here, for the EVIC class we call the device EVICTUS and assign the number 0x4400 to it.

In our object file EVIC.cpp, we have to alter our device constructor to include this.

EVIC::EVIC() : Device()

{

prefsHandler = new PrefHandler(EVICTUS);

commonName = "Andromeda Interfaces EVIC Display";

}

This registers us for the PrefsHandler to provide memcache space. We can then use LoadConfiguration and SaveConfiguration to handle our persistent data that we want to use from session to session without loss.

# MULTIPLE DEVICES ON CAN

GEVCU provides two independent CAN ports that can be configured for different speeds and operated more or less simultaneously. The nature of CAN is that a variety of hardware devices can be on the bus simultaneously as long as they all use the same data speed. And so of course a variety of object modules is envisioned, each servicing one or more CAN devices.

Again to accommodate this without chaos, we have developed a CAN handler. The CAN handler monitors the two CAN busses and when a CAN message is received, the message is passed to the appropriate module. And so each module performing CAN tasks must be registered with the CAN handler as to which specific CAN message IDs it wants to receive.

A canbus handler allows your device to register to receive frames that match the mask. The call to attach has four parameters. The first will basically always be “this”. The second is the ID to match, the third is the mask, and the fourth specifies whether you are interested in standard (false) or extended (true) frames.

canHandlerEv->attach(this, 0x230, 0x7f0, false);

canHandlerCar->attach(this, 0x650, 0x7f0, false);

In this case, we are registering with CAN bus 0 (Ev) to receive any message with an id between 0x230 and 0x23F.

We are also registering with CAN bus 1 (Car) to receive any CAN message with ID 0x650 through 0x65F.

If you need a quick refresher on masks and IDs: CAN bus filtering happens by taking every incoming frame and doing a bitwise AND with each registered mask in turn. The result of this is then compared to the associated ID for that mask. If the two match then your device will receive that frame. For instance, if a frame with 0x23D were to come in and the DmocMotorController had registered a mask of 0x7F0 and an ID of 0x230. 0x23D AND 0x7F0 = 0x230. This does match the ID and so DmocMotorController would get the frame.

Your class should have a handleCanFrame() method if you have registered one or more canbus handlers. This method takes a pointer to a CAN_FRAME structure as input.

# void DmocMotorController::handleCanFrame(CAN_FRAME *frame)

{

}

To send a frame, first create a CAN_FRAME structure variable, fill it out, and use sendFrame() to send it.

### CAN_FRAME output; //establishes variable output of structure CAN_FRAME

### output.length = 8; //Sets number of bytes in payload

### output.id = 0x207; //Sets message id

### output.extended = 0; //0 standard 11 bit frame 1 for extended 29bit frame

### output.data.bytes[0] = 0xa5; //This is simply puts value 5A

### output.data.bytes[1] = 0xa5; //in the first three payload bytes

### output.data.bytes[2] = 0x5a;

### output.data.bytes[3] = 0x00;

### output.data.bytes[4] = 0x00;

### output.data.bytes[5] = 0x00;

### output.data.bytes[6] = 0x00;

### output.data.bytes[7] = 0x00;

### CanHandler::getInstanceEV()->sendFrame(output); //Send the frame

IN this case we establish the variable output as type CAN_FRAME

We set the length to 8 bytes and the message ID to 0x207. We set it for standard 11bit frames and then populate the eight bytes with whatever we like. Then call the can handler to send frame OUTPUT. On the EV (CAN0) bus.

So note that we used a call to the can handler to register our ids and masks for incoming messages, and provided a method to handle those incoming messages by the specific name handleCanFrame.

We used another call to the canhandler to send a message we had preloaded into a CAN_FRAME variable.

In this way, all traffic is handled by the can handler and it can intelligently parse out CAN frames to hungry object modules waiting for them , and also stream messages onto the bus without collision or panic party.

The GEVCU project is designed such that the core system can be extended with modules that provide support for various pieces of hardware. Designing a new module is not conceptually complex but does require several things to be successful.

Note about formatting: BOLD words are class names. Italic words are file names. Underlined words are methods or members of a class. Methods are postfixed with ().

1. The first order of business is to find an existing module of hopefully the same basic type as your desired new module. For instance, if you hope to add support for an XYZ inverter then maybe you’d like to copy the DmocMotorController class. Rename the files with the same format. Maybe you’d name the files XYZMotorController.cpp and XYZMotorController.h If you cannot find an existing device of the same type then still use an existing set of files. The DmocMotorController class could be used as the basis for most any other device.
2. Rename all of the class references in the copied files as well.
3. Notice that DmocMotorController inherits from MotorController and CanObserver. If you are not creating a motor controller class then inherit from something else. Currently the other good choices are Throttle or Device. Device is always a decent choice if no more specific parent class exists. Inheriting from CanObserver is required if your device needs access to either of the CAN busses.
4. Each device can store data within EEPROM. Each device should create a configuration class that inherits from DeviceConfiguration. The loadConfiguration() and saveConfiguration() methods of DmocMotorController and MotorController can be used as a reference for how to load and save configurations.
5. Each device also must have a unique ID and should set what type of device it is. These are set with getId() and getType(). There is a global list of IDs that you should add your device to. DeviceTypes.h contains both the allowable device types and the ID of each and every device that is compiled into the firmware. You will note that DmocMotorController does not contain getType(). Instead it maintains the parent class version since it is still a motor controller.
6. Next, edit the constructor. Most of the constructor will be custom to your device but you will need to set prefsHandler to use your device ID constant instead of DMOC645. Also, set commonName to a nice, short description of your device.
7. Then there are several edits to make in the setup method. As shown in the DmocMotorController class, one should set up the tick handler, load the EEPROM configuration, call the parent setup (if applicable), and set up canbus handlers (if applicable).
  a. A tick handler allows your device to receive periodic ticks so that it can do processing at set intervals. This might be so that you can send canbus frames or so that you can check for input on one or more pins.
  b. Your class should have a handleTick() method if you have registered a tick handler.
  c. A canbus handler, handleCanFrame(), allows your device to register to receive frames that match the mask. The call to attach has four parameters. The first will basically always be “this”. The second is the ID to match, the third is the mask, and the fourth specifies whether you are interested in standard (false) or extended (true) frames. If you need a quick refresher on masks and IDs: Canbus filtering happens by taking every incoming frame and doing a bitwise AND with each registered mask in turn. The result of this is then compared to the associated ID for that mask. If the two match then your device will receive that frame. For instance, if a frame with 0x23D were to come in and the DmocMotorController had registered a mask of 0x7F0 and an ID of 0x230. 0x23D AND 0x7F0 = 0x230. This does match the ID and so DmocMotorController would get the frame.
  d. Your class should have a handleCanFrame() method if you have registered one or more canbus handlers. This method takes a pointer to a canbus frame as input.
8. As covered above, handleTick() and handleCanFrame() will form the majority of the action in most devices. Many devices will want to be able to send canbus frames out as well. This is done through CanHandler::getInstanceEV() or CanHandler::getInstanceCar(). The MotorController class pre-caches CanHandler::getInstanceEV() into the canHandlerEv member. To send a frame, first create a CAN_FRAME variable, fill it out, and use sendFrame() to send it. The DMOC sendCmd1 method shows how to do this.
9. If your device handler needs access to physical IO then use the systemIO member variable inherent to all devices. This variable references the SystemIO class which has the ability to interact with all of the digital I/O and analog inputs.
10. Now that the device handler has been constructed it is time to connect it with the rest of the system. In GEVCU.ino there is a function called createObjects(). You will need to instantiate your class here. You will also have you add your .h file as an include in GEVCU.h. With this done everything should automatically work. The system uses the PrefsHandler instance you setup in the class constructor to determine whether a given device is enabled and only sets up devices which are enabled.
11. A consequence of above is that you *must* enable your new device before it will do anything. This is done by typing “ENABLE=” followed by the ID of your new device.
1. Create your object.cpp and object.h files for your class. Often it is of help to copy an existing file set and rename them. If your new object is a motorcontroller, for example, use dmocMotorController.cpp and dmocMotorController.h. If it is a charger, copy a charger module.
2. List your device in DeviceTypes.h
3. Add your device as an include in GEVCU.h
4. Revise the createObjects section of GEVCU.ino to instantiate your class there.

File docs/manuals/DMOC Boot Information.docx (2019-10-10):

DMOC Boot Information

EEBoxConfig: CRC OK. Versions Match.

CBL-51NA-3041-001

EE Parameters: CRC OK. GUID match OK.

EE3 (Vars): CRC OK. GUID match OK.

EEBoxConfig: CRC OK. Versions Match.

Control at 1x switching frequency (10kHz).

Azure Transit Connect MY10.5 645 Liquid Cooled, Siemens 1PV5135

P1X-18FB-3047-010 Fri Oct 28 16:07:19 2011

Compiled by zsobhani from b_rel_0032 at R21756+

Hardware PN: CTR-010180-00K SN: 111018-006

GUID: 9D-C7-1C-F3-A0-B7-42-DD

DMoC Time is: 2018/05/31 22:52:57 GMT

................"""""""""""""""""""""""""""""""""


NOTE: DMOC serial parameters are 19200 8N1

Note the GUID is the same as for my first DMOC

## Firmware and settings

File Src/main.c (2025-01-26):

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
/* Includes ------------------------------------------------------------------*/
#include "main.h"
#include "cmsis_os.h"
#include "usb_device.h"

/* USER CODE BEGIN Includes */
#include <string.h>
#include "SerialTaskSend.h"
#include "stm32f4xx_hal_pcd.h"
//#include "usbd_cdc_if.h"
#include "cdc_txbuff.h"
#include "CanTask.h"
#include "can_iface.h"
#include "canfilter_setup.h"
#include "stm32f4xx_hal_can.h"
#include "getserialbuf.h"
#include "stackwatermark.h"
#include "yprintf.h"
#include "gateway_comm.h"
#include "gateway_CANtoPC.h"
#include "DTW_counter.h"
#include "SerialTaskReceive.h"
#include "yscanf.h"
#include "adctask.h"
#include "ADCTask.h"
#include "adcparams.h"
#include "adcparamsinit.h"
#include "gateway_PCtoCAN.h"
#include "morse.h"
#include "MailboxTask.h"
#include "GatewayTask.h"
#include "iir_f2.h"
#include "spiserialparallelSW.h"
#include "cdc_txbuff.h"
#include "SpiOutTask.h"
#include "BeepTask.h"
#include "lcdprintf.h"
#include "LEDTask.h"
#include "led_chasing.h"
#include "calib_control_lever.h"
#include "lcdmsg.h"
#include "dmoc_control.h"
#include "LcdTask.h"
#include "lcd_hd44780_i2c.h"
#include "LcdmsgsTask.h"
#include "LcdmsgsetTask.h"
#include "CID004Task.h"


/* USER CODE END Includes */

/* USER CODE BEGIN PTD */

void* verr[8];
uint32_t verrx = 0;
__attribute__( ( always_inline ) ) __STATIC_INLINE uint32_t __get_SP(void) 
{ 
  register uint32_t result; 

  __ASM volatile ("MOV %0, SP\n" : "=r" (result) ); 
  return(result); 
} 

uint32_t timectr = 0;
struct CAN_CTLBLOCK* pctl0;	// Pointer to CAN1 control block
struct CAN_CTLBLOCK* pctl1;	// Pointer to CAN2 control block

uint32_t debugTX1b;
uint32_t debugTX1b_prev;

uint32_t debugTX1c;
uint32_t debugTX1c_prev;

uint32_t debug03;
uint32_t debug03_prev;

extern osThreadId SerialTaskHandle;
extern osThreadId CanTxTaskHandle;
extern osThreadId CanRxTaskHandle;
extern osThreadId SerialTaskReceiveHandle;
extern osThreadId GatewayTaskHandle;

uint16_t m_trap = 450; // Trap codes for MX Init() and Error Handler

uint8_t canflag;
uint8_t canflag1;
uint8_t canflag2;

uint8_t lcdflag = 0;

/* USER CODE END PTD */

ADC_HandleTypeDef hadc1;
DMA_HandleTypeDef hdma_adc1;

CAN_HandleTypeDef hcan1;

I2C_HandleTypeDef hi2c1;
DMA_HandleTypeDef hdma_i2c1_tx;
DMA_HandleTypeDef hdma_i2c1_rx;

SPI_HandleTypeDef hspi2;

TIM_HandleTypeDef htim1;

UART_HandleTypeDef huart2;
UART_HandleTypeDef huart3;
UART_HandleTypeDef huart6;
DMA_HandleTypeDef hdma_usart2_rx;
DMA_HandleTypeDef hdma_usart2_tx;
DMA_HandleTypeDef hdma_usart3_rx;
DMA_HandleTypeDef hdma_usart3_tx;
DMA_HandleTypeDef hdma_usart6_rx;
DMA_HandleTypeDef hdma_usart6_tx;

osThreadId defaultTaskHandle;
osTimerId defaultTaskTimerHandle;
void SystemClock_Config(void);
static void MX_GPIO_Init(void);
static void MX_DMA_Init(void);
static void MX_USART6_UART_Init(void);
static void MX_USART2_UART_Init(void);
static void MX_CAN1_Init(void);
static void MX_ADC1_Init(void);
static void MX_SPI2_Init(void);
static void MX_USART3_UART_Init(void);
static void MX_TIM1_Init(void);
static void MX_I2C1_Init(void);
void StartDefaultTask(void const * argument);
void CallbackdefaultTaskTimer(void const * argument);

/* USER CODE BEGIN PFP */

/* Detect the processor ID. GevcurStates uses this. */
#define Unique_device_ID_register 0x1fff7a10 // DEH rig ID
uint32_t deh_rigid[3] = {0x00260027, 0x3131470e, 0x31343533};
uint32_t this_rig_id[3];
uint8_t deh_rig; // 3 = deh's f4 rig; != 3 means not deh's f4; 

/* USER CODE END PFP */

/**
  * @brief  The application entry point.
  * @retval int
  */
int main(void)
{

  /* USER CODE BEGIN 1 */
	BaseType_t ret;	   // Used for returns from function calls
	osMessageQId Qidret; // Function call return
	osThreadId Thrdret;  // Return from thread create

// Debug: Clear heap area
//uint32_t* pclr = (uint32_t*)(0x2000bb80);
//while (pclr < (uint32_t*)(0x2000bb80 + 32768)) *pclr++ = 0x66666666;

  /* USER CODE END 1 */

  /* MCU Configuration--------------------------------------------------------*/

  /* Reset of all peripherals, Initializes the Flash interface and the Systick. */
  HAL_Init();

  /* USER CODE BEGIN Init */
	DTW_counter_init();

  uint32_t* prigid =(uint32_t*)Unique_device_ID_register;
  uint32_t* pdehrig = &deh_rigid[0];
  for (int i = 0; i < 3; i++)
  {
    if (*pdehrig == *prigid)
      deh_rig += 1;
  }

  /* USER CODE END Init */

  /* Configure the system clock */
  SystemClock_Config();

  /* USER CODE BEGIN SysInit */
	/* Add bcb circular buffer to SerialTaskSend for uart6 -- LCD */
	#define NUMCIRBCB6  16 // Size of circular buffer of BCB for uart6
	ret = xSerialTaskSendAdd(&HUARTLCD, NUMCIRBCB6, 1); // dma
	if (ret < 0) morse_trap(1); // Panic LED flashing

	/* Add bcb circular buffer to SerialTaskSend for usart2 -- gateway */
	#define NUMCIRBCB2  16 // Size of circular buffer of BCB for usart2
	ret = xSerialTaskSendAdd(&huart2, NUMCIRBCB2, 1); // dma
	if (ret < 0) morse_trap(2); // Panic LED flashing

	/* Add bcb circular buffer to SerialTaskSend for usart3 -- PC monitor */
	#define NUMCIRBCB3  16 // Size of circular buffer of BCB for usart3
	ret = xSerialTaskSendAdd(&HUARTMON, NUMCIRBCB3, 1); // dma
	if (ret < 0) morse_trap(14); // Panic LED flashing

	/* Setup TX linked list for CAN  */
   // CAN1 (CAN_HandleTypeDef *phcan, uint8_t canidx, uint16_t numtx, uint16_t numrx);
	pctl0 = can_iface_init(&hcan1, 0, 32, 64);
	if (pctl0 == NULL) morse_trap(7); // Panic LED flashing
	if (pctl0->ret < 0) morse_trap(77);

	// CAN 2
#ifdef CONFIGCAN2
	pctl1 = can_iface_init(&hcan2, 1,32, 64);
	if (pctl1 == NULL) morse_trap(8); // Panic LED flashing
	if (pctl1->ret < 0) morse_trap(88);
#endif

  /* USER CODE END SysInit */

  /* Initialize all configured peripherals */
  MX_GPIO_Init();
  MX_DMA_Init();
  MX_USART6_UART_Init();
  MX_USART2_UART_Init();
  MX_CAN1_Init();
  MX_ADC1_Init();
  MX_SPI2_Init();
  MX_USART3_UART_Init();
  MX_TIM1_Init();
  MX_I2C1_Init();
  /* USER CODE BEGIN 2 */

/*
DiscoveryF4 LEDs --
 GPIOD, GPIO_PIN_12 GREEN
 GPIOD, GPIO_PIN_13 ORANGE
 GPIOD, GPIO_PIN_14 RED
 GPIOD, GPIO_PIN_15 BLUE
*/
  /* USER CODE END 2 */

  /* USER CODE BEGIN RTOS_MUTEX */
  /* add mutexes, ... */
  /* USER CODE END RTOS_MUTEX */

  /* USER CODE BEGIN RTOS_SEMAPHORES */
  /* add semaphores, ... */
  /* USER CODE END RTOS_SEMAPHORES */

  /* Create the timer(s) */
  /* definition and creation of defaultTaskTimer */
  osTimerDef(defaultTaskTimer, CallbackdefaultTaskTimer);
  defaultTaskTimerHandle = osTimerCreate(osTimer(defaultTaskTimer), osTimerPeriodic, NULL);

  /* USER CODE BEGIN RTOS_TIMERS */
  /* start timers, add new ones, ... */

	/* defaultTask timer for pacing defaultTask output. */
//	ret = xTimerChangePeriod( defaultTaskTimerHandle  ,pdMS_TO_TICKS(64),0);

  /* USER CODE END RTOS_TIMERS */

  /* USER CODE BEGIN RTOS_QUEUES */
  /* add queues, ... */

  /* USER CODE END RTOS_QUEUES */

  /* Create the thread(s) */
  /* definition and creation of defaultTask */
  osThreadDef(defaultTask, StartDefaultTask, osPriorityNormal, 0, 448);
  defaultTaskHandle = osThreadCreate(osThread(defaultTask), NULL);

  /* USER CODE BEGIN RTOS_THREADS */
  /* add threads, ... */
/* =================================================== */
  /* init code for USB_DEVICE */

//taskENTER_CRITICAL();
//  MX_USB_DEVICE_Init();
//taskEXIT_CRITICAL();


	/* Create serial task (priority) */
	// Task handle "osThreadId SerialTaskHandle" is global
	Thrdret = xSerialTaskSendCreate(osPriorityNormal+0);	// Create task and set Task priority
	if (Thrdret == NULL) morse_trap(225);

	/* Create serial receiving task. */
	ret = xSerialTaskReceiveCreate(osPriorityNormal+0);
	if (ret != pdPASS) morse_trap(224);

	/* Setup semaphore for yprint and sprintf et al. */
	yprintf_init();

	/* USB-CDC buffering */
	#define NUMCDCBUFF 4	// Number of CDC task local buffers
	#define CDCBUFFSIZE 64*4	// Best buff size is multiples of usb packet size
	struct CDCBUFFPTR* pret;
	pret = cdc_txbuff_init(NUMCDCBUFF, CDCBUFFSIZE); // Setup local buffers
	if (pret == NULL) morse_trap(223);
	
	/* USB-CDC queue and task creation */
	Qidret = xCdcTxTaskSendCreate(osPriorityNormal+0); // arg = Priority level
	if (Qidret < 0) morse_trap(221); // Panic LED flashing

  /* definition and creation of CanTxTask - CAN driver TX interface. */
  Qidret = xCanTxTaskCreate(osPriorityNormal+2, 64); // CanTask priority, Number of msgs in queue
	if (Qidret < 0) morse_trap(220); // Panic LED flashing

  /* definition and creation of CanRxTask - CAN driver RX interface. */
  /* The MailboxTask takes care of the CANRx                         */
//  Qidret = xCanRxTaskCreate(1, 32); // CanTask priority, Number of msgs in queue
//	if (Qidret < 0) morse_trap(6); // Panic LED flashing

	/* Setup CAN hardware filters to default to accept all ids. */
	HAL_StatusTypeDef Cret;
	Cret = canfilter_setup_first(0, &hcan1, 15); // CAN1
	if (Cret == HAL_ERROR) morse_trap(219);

#ifdef CONFIGCAN2
	Cret = canfilter_setup_first(1, &hcan2, 15); // CAN2
	if (Cret == HAL_ERROR) morse_trap(217);
#endif

	/* Remove "accept all" CAN msgs and add specific id & mask, or id here. */
	// See canfilter_setup.h

	/* Create MailboxTask */
	xMailboxTaskCreate(osPriorityNormal+2); // (arg) = priority

	/* Create GatewayTask */
	xGatewayTaskCreate(osPriorityNormal+1); // (arg) = priority

	/* GEVCUr state machine. */
	Thrdret = xGevcuTaskCreate(osPriorityNormal+2); // (arg) = priority
	if (Thrdret == NULL) morse_trap(216);

	/* Create Mailbox control block w 'take' pointer for each CAN module. */
	struct MAILBOXCANNUM* pmbxret;
	// (CAN1 control block pointer, size of circular buffer)
	pmbxret = MailboxTask_add_CANlist(pctl0, 48);
	if (pmbxret == NULL) morse_trap(215);

#ifdef CONFIGCAN2
	// (CAN2 control block pointer, size of circular buffer)
	pmbxret = MailboxTask_add_CANlist(pctl1, 48); // Use default buff size
	if (pmbxret == NULL) morse_trap(214);
#endif

	/* Further initialization of mailboxes takes place when tasks start */

	/* Select interrupts for CAN1 */
	HAL_CAN_ActivateNotification(&hcan1, \
		CAN_IT_TX_MAILBOX_EMPTY     |  \
		CAN_IT_RX_FIFO0_MSG_PENDING |  \
		CAN_IT_RX_FIFO1_MSG_PENDING    );

	/* Select interrupts for CAN2 */
#ifdef CONFIGCAN2
	HAL_CAN_ActivateNotification(&hcan2, \
		CAN_IT_TX_MAILBOX_EMPTY     |  \
		CAN_IT_RX_FIFO0_MSG_PENDING |  \
		CAN_IT_RX_FIFO1_MSG_PENDING    );
#endif

	/* Switch logic from queue loaded by Spi interrupts. */
//	Thrdret = xSwitchTaskCreate(1);
//	if (Thrdret == NULL) morse_trap(20); // Panic LED flashing

	/* Spi shift register task. */
	Thrdret = xSpiOutTaskCreate(osPriorityNormal+1);
	if (Thrdret == NULL) morse_trap(213); // Panic LED flashing

	/* Beeper task (taskpriority, beepqsize) */
	Thrdret = xBeepTaskCreate(osPriorityNormal+0, 32);
	if (Thrdret == NULL) morse_trap(212); // Panic LED flashing

	/* LED task (taskpriority, max queued items) .*/
	Thrdret = xLEDTaskCreate(osPriorityNormal+0, 32);
	if (Thrdret == NULL) morse_trap(211); // Panic LED flashing

	/* ADC summing, calibration, etc. */
	xADCTaskCreate(osPriorityNormal+1); // (arg) = priority

	/* Start SPI for switch/led shift register. */
	if (spiserialparallel_init(&hspi2) != HAL_OK) morse_trap(49);

	/* Queue for running LCD out of defaultTask. */
	Qidret = lcdmsg_init(16);
	if (Qidret < 0) morse_trap(210); // Panic LED flashing

  /* LCD I2C: message handling. (taskpriority, number buffers). */
  osThreadId retThrd =  xLcdTaskCreate(osPriorityNormal+0,32);
  if (retThrd == NULL) morse_trap(123);

  /* LCD I2C: message generation (calls to 'printf or'puts). 
  'printf and overrun stalls take place in this task.  
  (task priority, number in queue of pointer|union) */
  retThrd= xLcdmsgsetTaskCreate(osPriorityNormal+0,32);
  if (retThrd == NULL) morse_trap(125);  

  /* CAN ID004 sending task. */
  retThrd = xCID004TaskCreate(osPriorityNormal+0);
  if (retThrd == NULL) morse_trap(131);

  /* Set switches before tasks begin running. */
  calib_control_lever_init();
  GevcuTask_init_switches();

  /* init code for USB_DEVICE */
#ifdef USEUSBFORCANMSGS
  taskENTER_CRITICAL();
    MX_USB_DEVICE_Init();
  taskEXIT_CRITICAL();
#endif  

/* =================================================== */

  /* USER CODE END RTOS_THREADS */

  /* Start scheduler */
  osKernelStart();

  /* We should never get here as control is now taken by the scheduler */

  /* Infinite loop */
  /* USER CODE BEGIN WHILE */
  while (1)
  {
    /* USER CODE END WHILE */

    /* USER CODE BEGIN 3 */
  }
  /* USER CODE END 3 */
}

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
/* USER CODE BEGIN 4 */

static struct LCDMSGSET lcdi2cfunc1;
// LCD splash screen                                                        "12345678901234567890"
static void lcdi2cmsgm1    (union LCDSETVAR u){lcdi2cputs  (&punitd4x20,0,0,"GEVCUr   250126:1130");}
static void lcdi2cmsgm1deh (union LCDSETVAR u){lcdi2cputs  (&punitd4x20,0,0,"GEVCUrDeh250126:1130");}

/* USER CODE END 4 */

/* USER CODE BEGIN Header_StartDefaultTask */
/**
  * @brief  Function implementing the defaultTask thread.
  * @param  argument: Not used 
  * @retval None
  */
// ################################################################################
// ######### DEFAULT TASK #########################################################
// ################################################################################
/* USER CODE END Header_StartDefaultTask */
void StartDefaultTask(void const * argument)
{
  /* init code for USB_DEVICE */
  MX_USB_DEVICE_Init();
  /* USER CODE BEGIN 5 */

osDelay(50); // Debugging HardFault

/* Select code for testing/monitoring by uncommenting #defines */
//#define DISPLAYSTACKUSAGEFORTASKS
//#define SHOWEXTENDEDSUMSOFADCRAWREADINGS
//#define SHOWSUMSOFADCRAWREADINGS
//#define SHOWINCREASINGAVERAGEOFADCRAWREADINGS
//#define SHOWSERIALPARALLELSTUFF
//#define STARTUPCHASINGLEDS
//#define TESTBEEPER
//#define SENDCANTESTMSGSINABURST
//#define SHOWADCCOMMONCOMPUTATIONS
//#define TESTLCDPRINTF
#define DMOCTESTS

	#define DEFAULTTSKBIT00	(1 << 0)  // Task notification bit for sw timer: stackusage
	#define DEFAULTTSKBIT01	(1 << 1)  // Task notification bit for sw timer: something else

	/* A notification copies the internal notification word to this. */
	uint32_t noteval = 0;    // Receives notification word upon an API notify

	/* notification bits processed after a 'Wait. */
	uint32_t noteused = 0;

	struct SERIALSENDTASKBCB* pbuf1 = getserialbuf(&HUARTMON,96);
	if (pbuf1 == NULL) morse_trap(11);

	struct SERIALSENDTASKBCB* pbuf3 = getserialbuf(&HUARTMON,96);
	if (pbuf3 == NULL) morse_trap(13);

	struct SERIALSENDTASKBCB* pbuf2 = getserialbuf(&HUARTMON,96);
	if (pbuf2 == NULL) morse_trap(12);

	struct SERIALSENDTASKBCB* pbuf4 = getserialbuf(&HUARTMON,96);	
	if (pbuf4 == NULL) morse_trap(12);

#ifdef TESTLCDPRINTF
	struct SERIALSENDTASKBCB* pbuflcd = getserialbuf(&HUARTLCD,64);
	if (pbuflcd == NULL) morse_trap(12);

	uint32_t lcdrow = 0;
	uint32_t lcdctr = 0;
	uint32_t lcdret = 0;
	
#endif

#ifdef DISPLAYSTACKUSAGEFORTASKS
	int ctr = 0; // Running count
	uint32_t heapsize;
	uint32_t showctr = 0;
	uint32_t t1_DSUFT; // DTW time  
	uint32_t t2_DSUFT = 0;
#endif

#ifdef SENDCANTESTMSGSINABURST
	/* Test CAN msg */
	struct CANTXQMSG testtx;
	testtx.pctl = pctl0;
	testtx.can.id = 0xc2200000;
	testtx.can.dlc = 8;
	int i;
	for (i = 0; i < 8; i++)
		testtx.can.cd.uc[i] = 0x30 + i;
	testtx.maxretryct = 8;
	testtx.bits = 0;
#endif

 /* LCD I2C msgs used in this task. */
  // Wait for LcdTask to instantiate 4x20 #1 unit. */
  uint8_t loopctr = 0;
  while ((punitd4x20 == NULL) && (loopctr++ < 10)) osDelay(10);
      if (punitd4x20 == NULL) morse_trap(2326);

  // Initial "splash:" msg on line 1 of lcdi2c 4x20 #1 display
  if (deh_rig == 3) // 3 = deh's f4 rig; != 3 means not deh's f4; )
    lcdi2cfunc1.ptr = lcdi2cmsgm1deh;
  else
    lcdi2cfunc1.ptr = lcdi2cmsgm1;

  if (LcdmsgsetTaskQHandle == NULL) morse_trap(2323);
    xQueueSendToBack(LcdmsgsetTaskQHandle, &lcdi2cfunc1, 0);   


HAL_GPIO_TogglePin(GPIOD,GPIO_PIN_15); // BLUE LED


#ifdef SHOWSUMSOFADCRAWREADINGS
extern uint32_t adcsumdb[ADC1IDX_ADCSCANSIZE]; // debug
extern uint32_t adcdbctr;    // debug
uint32_t adcdbctr_prev = adcdbctr;
uint16_t hdrctr = 999;
#endif


#ifdef SHOWEXTENDEDSUMSOFADCRAWREADINGS
uint16_t idx_xsum_prev = 0;
uint16_t hdrctr2 = 999;
#endif


#ifdef SHOWINCREASINGAVERAGEOFADCRAWREADINGS
float  fxxsum[ADC1IDX_ADCSCANSIZE];
float ftmp;
uint64_t xxsum[ADC1IDX_ADCSCANSIZE];
uint32_t ravectr = 0;
float frecip;
uint16_t idx_xxsum_prev = 0;
uint16_t hdrctr3 = 999;
uint8_t ix;
for (ix = 0; ix < ADC1IDX_ADCSCANSIZE; ix++) xxsum[ix] = 0;
#endif

#ifdef  SHOWSERIALPARALLELSTUFF
uint32_t spispctr_prev = 0;
#endif

#ifdef STARTUPCHASINGLEDS
struct LEDREQ spiledx;
spiledx.bitnum = 0; // Start with bit 0
struct LEDREQ spiledx_prev;
spiledx_prev.bitnum = 15; // Sart with previous bit 15
uint8_t chasectr = 0; // Counter for slowing down output rate
#endif

// Assure CL state
clfunc.state = INITLCD;


#ifdef TESTBEEPER
struct BEEPQ beepqtest;
beepqtest.duron  = 100;
beepqtest.duroff = 50;
beepqtest.repct  = 2;
//	HAL_TIM_PWM_Start(&htim1, TIM_CHANNEL_1);  
#endif

/* Purpose: flag to have other task wait before 'for' loop. */
lcdflag = 1;

/* Countdown timer for various display speeds. */
uint16_t slowtimectr = 0; // Approx 1/sec
uint16_t medtimectr = 0;  // Approx 8/sec

osDelay(50);
yprintf(&pbuf4,"\n\n\r##########..Start GEVCUr..#########");
if (deh_rig == 3)
  yprintf(&pbuf1,"\n\r... DEH f4 detected ......\n\r");
else
  yprintf(&pbuf1,"\n\r... Assume rig has contactor attached ......\n\r");


slowtimectr = 128;

osDelay(5);

	xTimerChangePeriod( defaultTaskTimerHandle,pdMS_TO_TICKS(63),0);
// ===== BEGIN FOR LOOP ==============================

	for ( ;; )
	{
		xTaskNotifyWait(noteused, 0, &noteval, portMAX_DELAY);
//    xTaskNotifyWait(0,0xffffffff, &noteval, portMAX_DELAY);
		noteused = 0;
		if ((noteval & DEFAULTTSKBIT00) != 0)
		{
			noteused |= DEFAULTTSKBIT00;
// ================= Higest rate =======================================
			/* Check each LED until CL calibration ends. */
			led_chasing();

			/* Update CL position on LCD after CL calibration ends. */
			lcdout();

			/* LCD output from queue pointers. */
			lcdmsg_poll();

#ifdef DMOCTESTS
	yprintf(&pbuf1,"\n\rSTATE:dmoc:act: %X new: %X : rep: %X :op: %X",dmocctl[0].dmocstateact,dmocctl[0].dmocstatenew,dmocctl[0].dmocstaterep,dmocctl[0].dmocopstate);
  yprintf(&pbuf2," speedact %6d",dmocctl[0].speedact);
#endif
	
// ================== SLOW ==============================================
/* Countdown timer notifications. */
			slowtimectr += 1;
			if (slowtimectr >= 64)
			{
				slowtimectr = 0;
#ifdef TESTLCDPRINTF
extern uint32_t lcddbg;
		lcdret = lcdprintf(&pbuflcd,lcdrow,0,"\n\r01234 %2d %3d %1d",lcdrow,lcdctr,lcddbg);
		lcdctr += 1;	lcdrow += 1; if (lcdrow >= 4) lcdrow = 0;
		lcdret = yprintf(&pbuf1,"\n\rlcdret: %d lcdctr: %d lcddbg: %d",lcdret, lcdctr,lcddbg);
#endif

#ifdef DISPLAYSTACKUSAGEFORTASKS
			/* Display the amount of unused stack space for tasks. */
    yprintf(&pbuf1,"\n\r");
t1_DSUFT = DTWTIME;
			showctr += 1; 
/* 'for' is to test doing all scans at one timer tick. */
for (showctr = 0; showctr < 15; showctr++)
{
				switch (showctr)
				{
/* Cycle through the tasks. */
case  0: stackwatermark_show(defaultTaskHandle,&pbuf1,"defaultTask--");break;
case  1: stackwatermark_show(SerialTaskHandle ,&pbuf2,"SerialTask---");break;
case  2: stackwatermark_show(CanTxTaskHandle  ,&pbuf3,"CanTxTask----");break;
case  3: stackwatermark_show(MailboxTaskHandle,&pbuf4,"MailboxTask--");break;
case  4: stackwatermark_show(ADCTaskHandle    ,&pbuf1,"ADCTask------");break;
case  5: stackwatermark_show(SerialTaskReceiveHandle,&pbuf2,"SerialRcvTask");break;
case  6: stackwatermark_show(GatewayTaskHandle,&pbuf3,"GatewayTask--");break;
case  7: stackwatermark_show(CdcTxTaskSendHandle,&pbuf4,"CdcTxTask----");break;
case  8: stackwatermark_show(SpiOutTaskHandle, &pbuf1,"SpiOutTask---");break;
case  9: stackwatermark_show(GevcuTaskHandle,  &pbuf2,"GevcuTask----");break;
case 10: stackwatermark_show(BeepTaskHandle,   &pbuf3,"BeepTask-----");break;
case 11: stackwatermark_show(LEDTaskHandle,    &pbuf4,"LEDTask------");break;
case 12: stackwatermark_show(LcdmsgsetTaskHandle,&pbuf1,"LcdmsgsetTask");break;
case 13: stackwatermark_show(LcdTaskHandle,    &pbuf1,"LcdTask------");break;

case 14:	heapsize = xPortGetFreeHeapSize(); // Heap usage (and test fp working.
			yprintf(&pbuf1,"\n\rGetFreeHeapSize: total: %i free %i %3.1f%% used: %i",configTOTAL_HEAP_SIZE, heapsize,\
				100.0*(float)heapsize/configTOTAL_HEAP_SIZE,(configTOTAL_HEAP_SIZE-heapsize)); break;
default: showctr=0; yprintf(&pbuf1,"\n\r%4i Unused Task stack space--", ctr++); break;
				}
}
yprintf(&pbuf3,"\n\rTIC DUR: %d", DTWTIME - t2_DSUFT);
t2_DSUFT = DTWTIME;
yprintf(&pbuf2,"\n\rDTW DUR: %d",t2_DSUFT - t1_DSUFT);
#endif


#ifdef TESTBEEPER
			xQueueSendToBack(BeepTaskQHandle,&beepqtest,portMAX_DELAY);

#endif

#ifdef  SENDCANTESTMSGSINABURST
			/* ==== CAN MSG sending test ===== */
			/* Place test CAN msg to send on queue in a burst. */
			/* Note: an odd makes the LED flash since it toggles on each msg. */
uint16_t ib;
			for (ib = 0; ib < 7; ib++)
				xQueueSendToBack(CanTxQHandle,&testtx,portMAX_DELAY);
#endif

#ifdef DEBUGGINGCDCREADINGFROMPC
/* Debugging CDC reading from PC */
extern uint32_t dbuggateway1;
extern uint32_t dbcdcrx;
extern uint32_t dblen;
extern uint32_t cdcifctr;
extern uint32_t dbrxbuff;
yprintf(&pbuf2,"\n\rdbuggateway1: %d dbcdcrx: %d dblen: %d cdcifctr: %d dbrxbuff: %d", dbuggateway1,dbcdcrx,dblen,cdcifctr,dbrxbuff);
#endif
  			}
// ================= Moderate ===================================
/* Countdown timer notifications. */
			medtimectr += 1;
			if (medtimectr >= 4)
			{
				medtimectr = 0;
			
/* ##### timer not counted down ##### */
		HAL_GPIO_TogglePin(GPIOD,GPIO_PIN_15); // BLUE LED
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

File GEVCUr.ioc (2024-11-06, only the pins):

Mcu.UserName=STM32F407VGTx
PA11.Signal=USB_OTG_FS_DM
PA12.Signal=USB_OTG_FS_DP
PA2.Signal=USART2_TX
PA3.Signal=USART2_RX
PA8.GPIO_Label=Beeper
PA8.Signal=S_TIM1_CH1
PB12.GPIO_Label=SPI2 NSS /CK
PB12.Signal=GPIO_Output
PB13.Signal=SPI2_SCK
PB14.Signal=SPI2_MISO
PB15.Signal=SPI2_MOSI
PB6.Signal=I2C1_SCL
PB7.Signal=I2C1_SDA
PC1.GPIO_Label=Control lever
PC1.Signal=ADCx_IN11
PC2.GPIO_Label=Supply 12v
PC2.Signal=ADCx_IN12
PC4.GPIO_Label=Supply 5v
PC4.Signal=ADCx_IN14
PC5.GPIO_Label=Spare
PC5.Signal=ADCx_IN15
PC6.Signal=USART6_TX
PC7.Signal=USART6_RX
PD0.Signal=CAN1_RX
PD1.Signal=CAN1_TX
PD12.GPIO_Label=LED GREEN
PD12.Signal=GPIO_Output
PD13.GPIO_Label=LED RED
PD13.Signal=GPIO_Output
PD14.GPIO_Label=LED ORANGE
PD14.Signal=GPIO_Output
PD15.GPIO_Label=LED BLUE
PD15.Signal=GPIO_Output
PD8.Signal=USART3_TX
PD9.Signal=USART3_RX
PE6.GPIO_Label=Beeper Drive
PE6.Signal=GPIO_Output
PH0-OSC_IN.Signal=RCC_OSC_IN
PH1-OSC_OUT.Signal=RCC_OSC_OUT

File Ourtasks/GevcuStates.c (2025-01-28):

/******************************************************************************
* File Name          : GevcuStates.c
* Date First Issued  : 07/01/2019
* Description        : States in Gevcu function w STM32CubeMX w FreeRTOS
*******************************************************************************/

#include "FreeRTOS.h"
#include "task.h"
#include "cmsis_os.h"
#include "malloc.h"
#include "ADCTask.h"
#include "adctask.h"
#include "LEDTask.h"
#include "GevcuEvents.h"
#include "GevcuStates.h"
#include "GevcuTask.h"
#include "calib_control_lever.h"
#include "contactor_control.h"
#include "yprintf.h"
#include "lcdprintf.h"
#include "gevcu_idx_v_struct.h"
#include "morse.h"
#include "adcparamsinit.h"
#include "lcdmsg.h"
#include "dmoc_control.h"
#include "dm1_idx_v_struct.h"
#include "control_law_v0.h"
#include "control_law_v1.h"
#include "control_law_v2.h"
#include "control_law_v3.h"
#include "LcdTask.h"
#include "LcdmsgsetTask.h"
#include "dm1_idx_v_struct.h"

#define GEVCULCDMSGDELAY 32 // Minimum number of time ticks between LCD msgs
#define GEVCULCDMSGLONG (128*30) // Very long delay

extern struct LCDI2C_UNIT* punitd4x20; // Pointer LCDI2C 4x20 unit
extern uint8_t deh_rig; // 3 == deh's f4 detected; not 3 == someone else's f4 

enum GEVCU_INIT_SUBSTATEA
{
	GISA_OTO,  
	GISA_WAIT,
};

/* Flag queue LCD msg only once. defaultTask will call these lcdprintf functions. */
static uint8_t msgflag = 0; // 0 = send; 1 = don't send
static uint8_t msgslow = 0; // Counter for pacing repeated msgs

/* *************************************************************************
 * void payloadfloat(uint8_t *po, float f);
 *	@brief	: Convert float to bytes and load into payload
 * @param	: po = pointer to payload byte location to start (Little Endian)
 * *************************************************************************/
void payloadfloat(uint8_t *po, float f)
{
	union FF
	{
		float f;
		uint8_t ui[4];
	}ff;
	ff.f = f; 

	*(po + 0) = ff.ui[0];
	*(po + 1) = ff.ui[1];
	*(po + 2) = ff.ui[2];
	*(po + 3) = ff.ui[3];
	return;
}

/* *************************************************************************
 * void GevcuStates_GEVCU_INIT(void);
 * @brief	: Initialization sequence: One Time Only
 * *************************************************************************/
//  20 chars will over-write all display chars from previous msg:       12345678901234567890
static void lcdi2cmsg1(union LCDSETVAR u){lcdi2cputs(&punitd4x20,           GEVCUTSK,0,"GEVCU_INT           ");}
static void lcdi2cmsg2a(union LCDSETVAR u){lcdi2cputs(&punitd4x20,           GEVCUTSK, 0,"SWITCH TO SAFE      ");}// LCD i2c

static uint8_t lmode_init; // Init switch
static uint8_t lmode; // Control law mode in use

 /* LCDI2C 4x20 msg. */
static struct LCDMSGSET lcdi2cfunc;

void GevcuStates_GEVCU_INIT(void)
{	
//	void (*ptr2)(void); // Pointer to queue LCD msg
	struct SWITCHPTR* p;

	uint8_t loopctr = 0;

	switch (gevcufunction.substateA)
	{
	case GISA_OTO: // Cycle Safe/Active sw.

		/* Wait for task that instantiates the LCD display. */
		while ((punitd4x20 == NULL) && (loopctr++ < 10)) osDelay(10);
  		if (punitd4x20 == NULL) morse_trap(235);

		msgflag = 0; // One-msg flag, JIC

		/* Wait for calib_control_lever.c to complete calibrations. */
		if (flag_clcalibed == 0) 
			break;

/* Control law mode. Selection hard coded. */
dmocctl[0].lmode = 3;	
lmode_init = 0;	

		/* Queue LCD msg to be sent once. */
		if (msgflag == 0)
		{ 
			msgflag = 1; // Don't keep banging away with the same msg

			// LCD I2C unit msg
			lcdi2cfunc.ptr = lcdi2cmsg1;
			// Place ptr to struct w ptr 
		 	if (LcdmsgsetTaskQHandle != NULL)
	  	  		xQueueSendToBack(LcdmsgsetTaskQHandle, &lcdi2cfunc, 0);
		}

		/* Update LED with SAFE/ACTIVE switch status. */
		p = gevcufunction.psw[PSW_PR_SAFE];
		gevcufunction.safesw_prev = p->db_on;
		switch (p->db_on)
		{
		case 1:
	      led_safe.mode = 0; // LED_SAFE off
			break;
			
		case 2:
	      led_safe.mode = 1; // LED_SAFE on
			break;
		}
		xQueueSendToBack(LEDTaskQHandle,&led_safe,portMAX_DELAY);
		msgflag = 0; // Allow next LCD msg to be sent once
		gevcufunction.substateA = GISA_WAIT;
		break;

	case GISA_WAIT: // More OTO to do here?
		if (gevcufunction.psw[PSW_PR_SAFE]->db_on == SWP_OPEN )
		{ // Here SAFE/ACTIVE switch is in ACTIVE position
			if (msgflag == 0)
			{ 
				msgflag = 1; // Don't keep banging away with the same msg
				lcdi2cfunc.ptr = lcdi2cmsg2a;
				if (LcdmsgsetTaskQHandle != NULL)
	 		   		xQueueSendToBack(LcdmsgsetTaskQHandle, &lcdi2cfunc, 0);
			}
			break;
		}

		/* Transition into safe mode,. */
		msgflag = 0; // Allow next LCD msg to be sent once
		msgslow = 255; // Pacing counter 
		gevcufunction.state = GEVCU_SAFE_TRANSITION;
		break;

		default:
			break;
	}
	return;
}
/* *************************************************************************
 * void GevcuStates_GEVCU_SAFE_TRANSITION(void);
 * @brief	: Peace and quiet, waiting for hapless Op.
 * *************************************************************************/
//  20 chars will over-write all display chars from previous msg:             12345678901234567890
static void lcdi2cmsg3a(union LCDSETVAR u){lcdi2cputs(&punitd4x20,GEVCUTSK,0,"GEVCU_SAFE_TRANSITIO");}
#if 0
static void lcdi2cmsg3b(union LCDSETVAR u){lcdi2cputs(&punitd4x20,GEVCUTSK,0,"WAIT CONTACTOR OPEN ");}
static void lcdi2cmsg3c(union LCDSETVAR u){lcdi2cputs(&punitd4x20,GEVCUTSK,0,"CONTACTOR NO-RESPONS");}
static void lcdi2cmsg3d(union LCDSETVAR u){lcdi2cputs(&punitd4x20,GEVCUTSK,0,"CONTACTOR NOT INITed");}
#endif

void GevcuStates_GEVCU_SAFE_TRANSITION(void)
{
//	void (*ptr2)(void) = &lcdmsg3; // LCD msg pointer

	if (msgflag == 0)
	{ 
		msgflag = 1; // Don't keep banging away with the same msg
		lcdi2cfunc.ptr = lcdi2cmsg3a; 
		 if (LcdmsgsetTaskQHandle != NULL)
	    	xQueueSendToBack(LcdmsgsetTaskQHandle, &lcdi2cfunc, 0);
	}
      led_safe.mode    = LED_BLINKFAST; // LED_SAFE blinking
		led_arm_pb.mode  = LED_OFF; // ARM Pushbutton LED
		led_arm.mode     = LED_OFF; // ARM LED
		led_prep_pb.mode = LED_OFF; // PREP Pushbutton LED
		led_prep.mode    = LED_OFF; // PREP LED
	xQueueSendToBack(LEDTaskQHandle, &led_safe   ,portMAX_DELAY);
	xQueueSendToBack(LEDTaskQHandle, &led_arm_pb ,portMAX_DELAY);
	xQueueSendToBack(LEDTaskQHandle, &led_arm    ,portMAX_DELAY);
	xQueueSendToBack(LEDTaskQHandle, &led_prep_pb,portMAX_DELAY);
	xQueueSendToBack(LEDTaskQHandle, &led_prep   ,portMAX_DELAY);

	/* Request contactor to DISCONNECT. */
	cntctrctl.req = CMDRESET;
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

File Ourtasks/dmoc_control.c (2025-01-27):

/******************************************************************************
* File Name          : dmoc_control.c
* Date First Issued  : 12/04/2019
* Board              : DiscoveryF4
* Description        : Control of dmoc unit [state machine version]
*******************************************************************************/
/* More formal state machine version. */

#include "dmoc_control.h"
#include "main.h"
#include "morse.h"
#include "DMOCchecksum.h"
#include "paycnvt.h"
#include "can_iface.h"
//#include "spiserialparallel.h"
#include "shiftregbits.h"
#include "calib_control_lever.h"
#include "dm1_idx_v_struct.h"

/* Name the indices to correspond to the GEVCU DMOC documentation. */
#define CMD1 0 
#define CMD2 1 
#define CMD3 2 

#define FALSE 1
#define TRUE  0

/* Command request bits assignments. 
Sourced location: ../dmoc/OurTasks/ContactorTask.h
*/

extern struct CAN_CTLBLOCK* pctl0;	// Pointer to CAN1 control block

/* struct holds "everything" for each DMOC. */
struct DMOCCTL dmocctl[NUMDMOC]; // Array allows for multiple DMOCs

/* ***********************************************************************************************************
 * void dmoc_control_initTORQUE(void); 
 * void dmoc_control_initSPEED(void);
 *
 * void dmoc_control_init(struct DMOCCTL* pdmocctl, uint8_t pwr_mode);
 * @brief   : Common init
 * @param   : pdmocctl = pointer with struct for DMOC instance
 * @param   : pwr_mode = enum PowerMode (DMOC_MODETORQUE or DMOC_MODESPEED)
 * @brief	: Prep dmoc(s)
 ************************************************************************************************************* */
void dmoc_control_init(struct DMOCCTL* pdmocctl, uint8_t pwr_mode)
{
	int i,j;

	pdmocctl->state        = DMOCINIT1; // Initial state
	pdmocctl->sendflag     = 0;
	pdmocctl->alive        = 0; // DMOC count increments by 2 & truncated
	pdmocctl->activityctr  = 0; // Count DMOC 0x476 (0x23B) incoming msgs
	pdmocctl->dmocstatefaulted = 0; // 1 = faulted
	pdmocctl->dmocnotsending   = 0; // 1 = dmoc CAN msgs not being received

	pdmocctl->activityctr_prev =   0; // Previous count (for computing difference)
	pdmocctl->activityctr      = 128; // Count CAN msgs from dmoc
	pdmocctl->activitytimctr   =  50; // Number of sw timer ticks between activity check
	pdmocctl->activitylimit    =   4; // Number dmoc CAN msgs received during interval

	pdmocctl->dmocstateact = DMOC_INIT; //DMOC_DISABLED;   // Assume initial state
	pdmocctl->dmocopstate  = DMOC_DISABLED;   // Requested startup state
	pdmocctl->dmocgear     = DMOC_NEUTRAL;    // Gear selection
	pdmocctl->pwr_mode     = pwr_mode; // Speed or Torque mode selection
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

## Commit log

2019-10-10 initial load
    [CP State LEDs.sch, Control Panel High Level.sch, MC Breakout-F4 & Power.sch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]
2019-10-12 save and backup work
    [ADC_rate.ods, adcsetup.ods, load-cell_calibration.ods]
2019-10-29 reading from ACM0 and outputting to gateway beginning to work, but multiple CAN id of zero indicating something wrong with circular buffering of msgs.
    [GatewayTask.c]
2019-11-01 solved problem with copying CAN struct causing a Hard Fault due to alignment. See GatewayTask.c
    [ADCTask.c, GEVCUr.ioc, GatewayTask.c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]
2019-11-05 save and backup after regeneration of code with updated STM32CubeMX version 5.4.0
2019-11-11 spi debugging for simulated control panel. shift reg in and out working. beeper and timer1 needs some cleanup. Unexplained hard faults upon startup still a buggaboo
    [GEVCUr.ioc, GatewayTask.c, main.c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]
2019-11-12 SpiOutTask added for spi shift register setting of bits. Input from shift register shows low order bit sometimes misses. Need to look at clock phasing
2019-11-13 save and backup. spiout and beeper tasks seem to work. Startup HardFault appears to be tied to stack usage printout in the default task, but maybe not
2019-11-15 save work. Fixed hw for shift register sclk drive. Hard Fault upon startup still a puzzle.
    [BeepTask.c, GevcuTask.c, main.c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]
2019-11-27 save and backup work. calib_control_lever routine with lcdprintf causing lockup with ASSERT on semaphore take. this version skips the lcdprintf. The CL calib not debugged, however.
    [ADCTask.c, GEVCUr.ioc, GevcuEvents.c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]
2019-11-28 calib_control_lever seems-to-work. Needs some tweaks for LCD instead of minicom. Beeper not working, and might be hardware
    [GevcuEvents.c, GevcuTask.c, GevcuTask.h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]
2019-11-30 save and backup work. Started work on keepalive for contactor in GevcuTask. Tweak beeper prompts in CL calibration. Startup HardFault still a buggaboo
    [BeepTask.c, GEVCUr.ioc, GatewayTask.c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]
2019-12-04 working on finding elusive bug. usb cdc buffer overflow likely. Save and back work
    [CanTask.c, can_iface.c, main.c]
2019-12-05 save and backup work. Possible fix to elusive bug. cdc_txbuff.c stepping _m pointer and not resetting work pointer to begin. No guarantees.
    [gevcu_func_init.c, main.c]
2019-12-24 spi shift register switch sorting out
    [swbox.scad]
2020-01-10 set beep pwm to 100%
2020-01-21 tested and rearranged spi bits to match gsm control panel
2020-01-21 add CL percent to uart in defaultTask for debugging LCD
2020-01-23 A fix in defaultTask for 111 hard fault. CL percentage monitor uart made more readable
    [ADCTask.c, CanTask.c, GatewayTask.c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]
2020-01-31 calib_control_lever--updated LCD msgs. Hysteresis is present. main.c updates CL pct after calibration.
2020-01-31 changed CL readings from adc sum to filtered adc sum
2020-02-03 LEDTask work. save and backup work
2020-02-07 SwitchTask added. safe-active switch logic but debounce not in place. Shifted calib_control_lever to be called from ADCTask to avoid double context switches by calling from GevcuTask.
    [ADCTask.c, GevcuTask.c, GevcuTask.h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]
2020-02-08 save and backup. SwitchTask development and test.
2020-02-09 LEDTask blinking works, but not fully tested.
2020-02-11 added led_chasing for sequencing CP leds. Increased sw debounce period.
2020-02-14 mode 0 for SwitchTask seems-to-work. mode 1 not done. USB init disabled for now.
2020-02-14 update debounce for z tension to 1 sec
2020-02-15 Update and save. pushbutton seems-to-work. switch pair unpdates will begin.
2020-02-18 SwitchTask, debouncing testing OK with two pushbuttons. Save and backup work
2020-02-18 SwitchTask, changed add debounce to add at list head
2020-02-18 minor change to SwitchTask before massive change to run it under interrupt
2020-02-19 Moved SwitchTask logic into spi interrupt callback and removed SwitchTask calls. spi interrupt callback not handled by spiserialparallelSW instead of spiserialparallel. Initial state of pushbutton, m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
    [main.c, spiserialparallel.c, spiserialparallelSW.c]
2020-02-20 save and back up. Added arm and prep pb w leds.
2020-02-21 save and backup work. Added HardFault_Handler asm code to save registers, patterned after FreeRTOS example. Switch initialization is now not correct.
    [main.c]
2020-02-21 save and backup. CL switch debouncing added as well as other small changes.
2020-02-23 save and backup. LEDTask with temp fix with full array scan for blinking, as linked list needs fixing. Net, it works but inefficient
    [LEDTask.c, main.c]
2020-02-24 Updated LED bit positions to match gsm CP. led_chasing sequence revision, all on all off at beginning and beep added at end of sequence.
2020-02-25 work on LEDTask, led_chasing, and switches
2020-02-26 save and backup. Added contactor_control_msg but currently not called.
2020-02-28 debugging. contacter not reconnecting and safe sw recycling fixed
    [GevcuEvents.c, GevcuStates.c, main.c]
2020-02-29 ELUSIVE BUG may have been found. CallbackdefaultTaskTimer in main, near line 1330, needed a check for a null defaultTaskHanle. Also, other GevcuTask led and sws revisions.
    [GevcuStates.c, SerialTaskReceive.c, main.c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]
2020-02-29 problem still with usb init. this time zeroing switches for init
    [main.c]
2020-02-29 minor change to LEDs in state
2020-02-29 update led
2020-03-02 mm changed to not flash if make fails
    [GevcuEvents.c, GevcuStates.c, main.c]
2020-03-03 save led fixes for GevcuStates
    [GatewayTask.c, GevcuStates.c, main.c]
2020-03-06 dmoc torque request only on in ARM state. Added morse_trap for MX Init failures
    [GevcuStates.c, dmoc_control.c, main.c]
2020-03-06 revert some dmoc torque request changes
    [GevcuStates.c]
2020-03-10 Change torquereq to float and Nm
2020-03-11 some rearrangements in dmoc_control. Changed pushbutton 0-1 to 0.0-0.01 so as to avoid extra multiplication.
    [GevcuEvents.c, GevcuStates.c, dmoc_control.c]
2020-03-13 debugging with live hookup. fixed ENABLE in dmoc_control
    [ADCTask.c, CanTask.c, GatewayTask.c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]
2020-03-13 dmoc debugging. state fix
    [dmoc_control.c]
2020-03-18 manual_inertia branch w z_tension pb reversing torque
    [GevcuStates.c, dmoc_control.c]
2020-03-18 anual_inertia positive and negative torque selection
2020-03-20 updates and minor fixes to manual_inertia branch
    [GevcuStates.c, GevcuTask.c, calib_control_lever.c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]
2020-03-22 dmoc_control.c revisions to deal with overspeed and retarding torque, and negative speeds, i.e. REVERSE gear
2020-03-24 fixed dmoc bugs. GEVCUBIT13 where speedact should have voltageact, and speed less than max should have been -max
    [dmoc_control.c]
2024-10-26 Convert LCD from UART to I2C, using code from stepper repo for I2C functions. This commit compiles but has not be flashed and run.
2024-10-27 more updates for switch to I2C
2024-10-28 compiles, dipslays flash screen on I2C lcd, and trap code 80 since no CL on deh rig
2024-10-29 IC2 trap 80 fix
    [calib_control_lever.c, main.c]
2024-10-30 debugging i2c lcd continues
2024-10-31 debugging I2C effect on led_chasing.
2024-11-01 fixed both switches ON with init in main
    [calib_control_lever.c, main.c, main.h]
2024-11-01 increase in LcdmsgsetTask fixed hard fault after lever calib
    [LcdmsgsetTask.c]
2024-11-01 fixed more switches to init in main.c
    [GevcuStates.c, GevcuTask.c, GevcuTask.h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]
2024-11-04 fix blinking continuing in SAFE mode.
    [GevcuEvents.c, GevcuStates.c, contactor_control_msg.c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]
2024-11-04 set beeper TIM1 pwm to 100 pct to test gsm beeper
2024-11-06 lcdmsgset.c had queue handle stepping on lcdmsg.c handle...same name. This may have cured the unexpected led problem
    [GEVCUr.ioc, GatewayTask.c, GevcuStates.c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]
2024-11-08 led_chasing.c and calib_control_lever.c interactin with LEDs fixed, but debug code to trace LED queue still in code.
    [GevcuEvents.c, GevcuStates.c, LEDTask.c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]
2024-11-09 removed debugging for leds with who = xx statements and array
2025-01-26 moved control_law_v1 params to params directory, plus other small changes
    [README-params.txt]
2025-01-26 fix control_law_v3, add mmf script
    [GevcuStates.c, main.c]
2025-01-28 Control Law 3 PREP LED tweaks

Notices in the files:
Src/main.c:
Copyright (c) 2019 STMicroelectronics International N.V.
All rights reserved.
